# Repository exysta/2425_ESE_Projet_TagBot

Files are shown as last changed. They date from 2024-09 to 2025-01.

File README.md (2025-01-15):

# 2425_ESE_Project_TagBot
Welcome to the TagBot project created by the amazing team consisted of Lucas Chapart, Charlotte Fricot and Marie Caronello.
The following description is in french but you can find the english description there but it is not up to date for now :

- [English](README_english.md)

  # Sommaire
  
1. [Introduction](#introduction)
2. [PCB](#pcb)
3. [Code](#code)

  # Introduction
  
Vous vous trouvez actuellement dans le projet TagBot (ou robot chat), qui s'intègre à un projet de classe où chaque équipe doit concevoir un robot. Ces robots doivent pouvoir jouer au chat ensemble, avec un chat et des souris, sur une table sans bords. 
  
Au terme de ce projet, notre chat robot doit pouvoir:
 - se déplacer sur une table sans bordure (sans tomber)
 - changer d'état (chat ou souris)
  - si le robot est chat, il doit pouvoir attraper la souris
  - si le robot est souris, il doit pouvoir échapper au chat
  
Nous avons plusieurs niveaux d'objectifs à atteindre : 
  - Niveau 0 : le robot se déplace + ne tombe pas de la table
  - Niveau 1 : détection d'un robot et s'en rapprocher (chat) ou s'en éloigner (souris)
  - Niveau 2 : changement de comportement après un contact + fonctionnement avec plusieurs robots
  - Niveau 3 : capacité de se localiser + ne pas être affecté par les obstacles hors de la table

  Le projet doit être réalisé sur un semestre, du mois de septembre au mois de janvier, avec un certain nombre de livrables à fournir avant chaque étape clé. Les   différentes étapes techniques incluent des phases de conception, de développement et de validation sur un système embarqué.

  <details>
  <summary><strong>Plan détaillé</strong></summary>  

  ### Avant les vacances de la Toussaint
  
  Les 10 premières séances sont consacrées à la création du PCB que l'on doit commander avant les vacances de la Toussaint. 
  
  - Séance 1 → Schéma architectural / BOM
  - Séance 2 et 3 → Schéma électronique annoté
  - Séance 4 → Corrections Schéma / BOM Finale
  - Séance 5 → Placement
  - Séance 6 → Placement corrigé
  - Séance 7 → Routage
  - Séance 8, 9 et 10 → Corrections Routage, export

  Dans le même temps, nous avons débuté la partie informatique avec la création du projet sur CubeIDE. Nous avons configuré les pins et commencé la rédaction des librairies pour les différents composants. 

  ### Entre la Toussaint et Noël

  Cette période est centrée sur le développement logiciel et l'intégration.

  ### Après les vacances de Noël

  L'accent est mis sur les derniers ajustements et les tests finaux avant la présentation. En effet, les dernières séances consacrées à ce projet vont nous permettre de finaliser les algorithmes de stratégie et les comportements robotiques. Le challenge final aura lieu le vendredi 10 janvier, ce challenge consistera en un test et une présentation du projet où tous les robots chats de notre classe s'affronteront.

   </details>

  ## Schéma architectural et materiel

<div align="center">
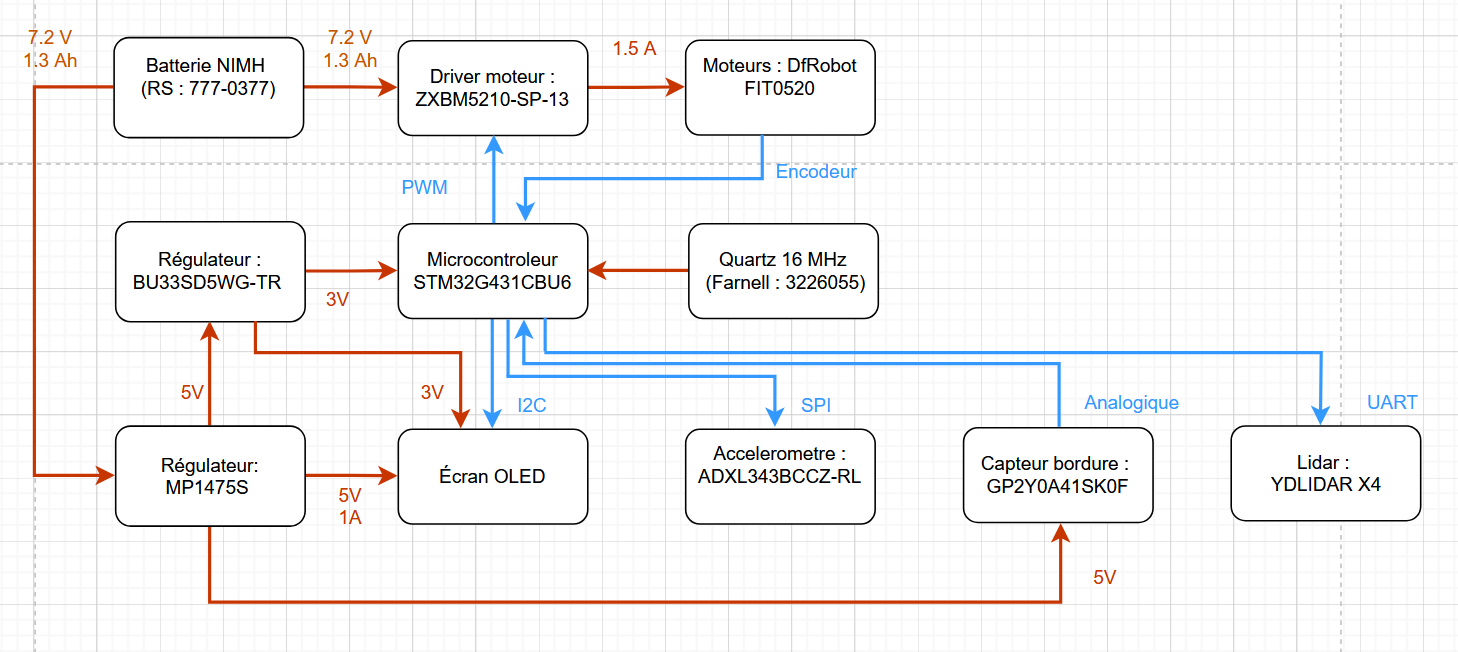
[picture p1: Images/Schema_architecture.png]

</div>
  
  L'essentiel du matériel a été imposé, mais il restait à déterminer le moyen par lequel le robot détecterait les bords pour éviter de tomber de la table. Pour cela, des capteurs infrarouges (IR) ont été choisis. Placés sous le robot, ces capteur reçoivent une tension qui détermine la distance par rapport au sol. Lorsque ce signal diminue fortement (ce qui correspond à une augmentation de la distance), cela indique la présence d'un bord. Étant donné que les capteurs sont situés sous le robot, il est nécessaire de détecter de faibles distances, comme le permet le capteur Sharp GP2Y0A21SK0F.

  Il est également envisagé d'ajouter une LED visible par l'utilisateur, permettant de connaître l'état du robot chat à tout moment.

  # PCB
  La première étape de la conception du PCB a été de réaliser le schéma électronique de la carte. Voici une liste des composants utilisés :

- **Microprocesseur** : STM32G431CBU6
- **Régulateurs de tension** : 5V et 3.3V
- **Drivers de moteurs** : ZXBM5210-SP-13
- **Système de batterie** : Batterie NIMH 7.2V 1.3Ah 
- **ST Link** : Interface de programmation et débogage
- **Oscillateur Quartz** : 16MHz
- **Connecteurs** : Divers connecteurs pour l'alimentation et les signaux
- **Accéléromètre** : ADXL343

## Détail des composants et branchements

### 1. Microprocesseur : STM32G431CBU6

Le microprocesseur STM32G431x6 est au cœur du robot. Il gère la logique du jeu et communique avec les autres composants. Le schéma de branchement du microprocesseur est disponible [ici](./Documents/datasheets/stm32g431cb.pdf).

<div align="center">
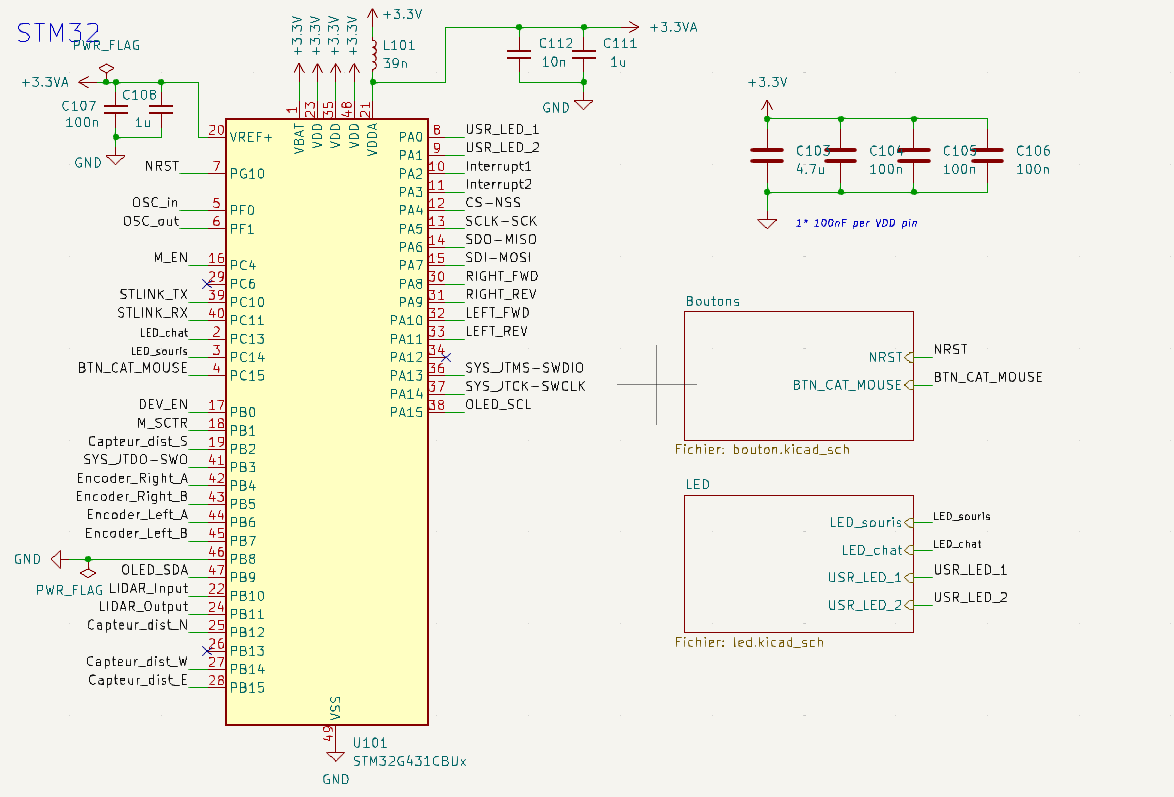
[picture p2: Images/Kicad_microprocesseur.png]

</div>

Les principaux branchements incluent :

- **VDDA** : Connecté à un filtrage LC pour lisser l'alimentation analogique.
- **VSS / VDD** : Alimentations principales.
- **GPIOs** : Utilisés pour le contrôle des LED de débogage et la communication avec les drivers de moteur.

Pour configurer les broches du microcontrôleur, le logiciel CubeIDE est utilisé. Une fois la configuration effectuée, la génération du fichier `.ioc` permet de documenter l'ensemble des options choisies pour chaque broche. Le fait d'utiliser l'ioc du microprocesseur permet de choisir au mieux chaque broche pour les entrée/sortie du microprocesseur.

### 2. LED

Le robot comporte 7 LEDs connectées à des résistances de limitation de courant.

- **Une LED rouge** : indique que le robot est le chat.
- **Une LED Bleue** : indique que le robot est une souris.
- **Deux LED vertes** : sont des LEDs de débogage.
- **Une LED jaune** : 5V
- **Une LED verte** : 3.3V
- **Une LED verte** : 7.2V

<div align="center">
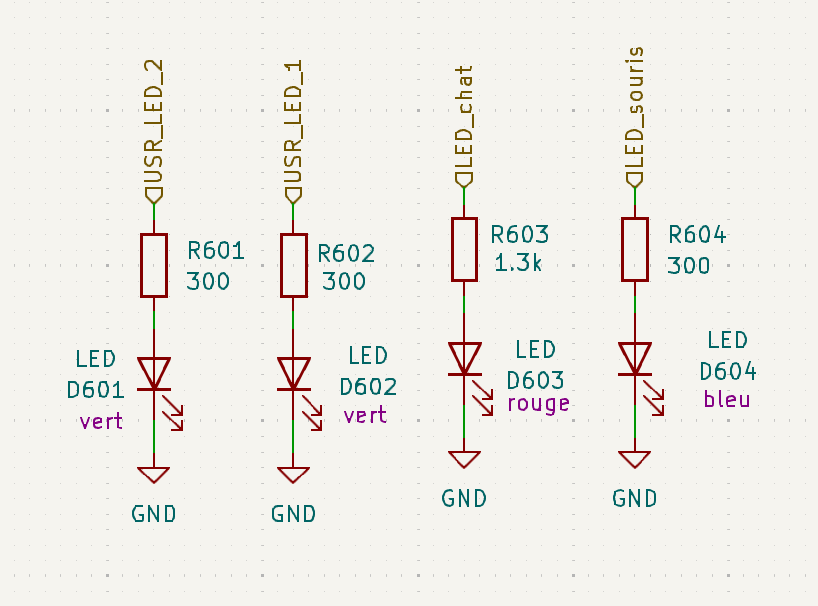
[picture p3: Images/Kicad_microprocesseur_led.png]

</div>

### 3. Boutons

Le robot dispose de deux boutons :

- **NRST** : Bouton de réinitialisation.
- **Mode** : Bouton qui permet de changer l'état du robot entre "chat" et "souris".

<div align="center">
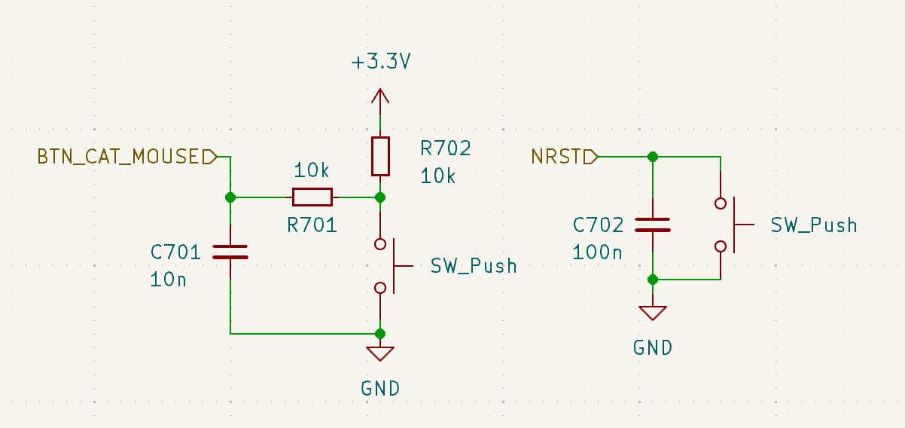
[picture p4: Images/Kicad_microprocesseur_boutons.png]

</div>

### 4. Drivers de Moteurs : ZXBM5210-SP-13

Les drivers de moteurs permettent de contrôler les moteurs à courant continu utilisés pour déplacer le robot. Le driver ZXBM5210 est connecté selon le schéma de la [documentation](./Documents/datasheets/driver_ZXBM5210.pdf).

<div align="center">
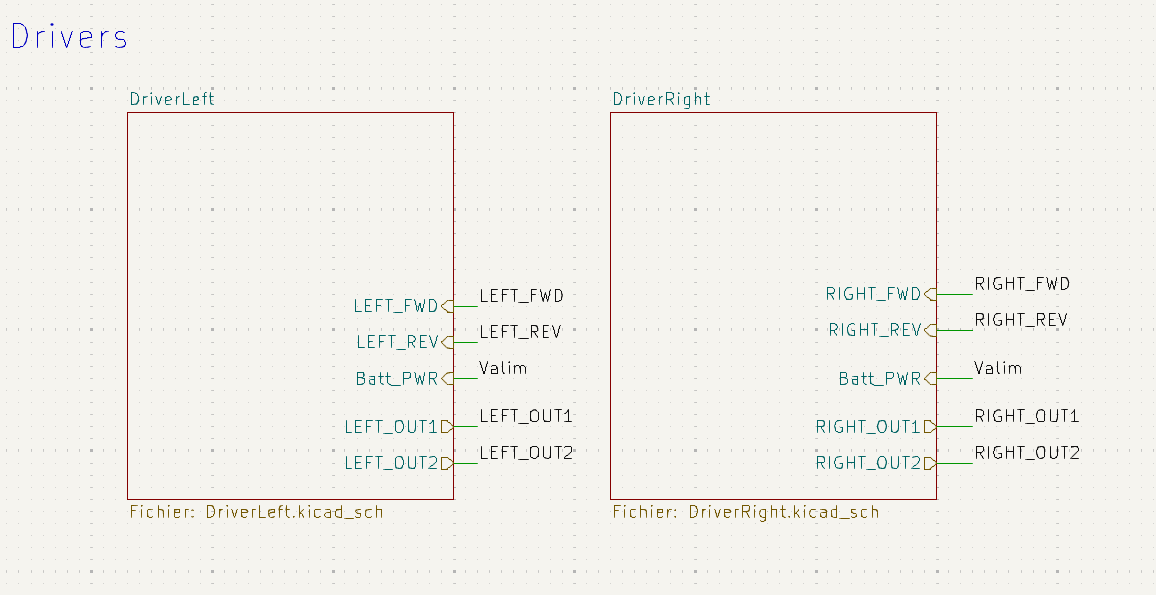
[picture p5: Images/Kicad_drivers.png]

</div>

Le branchement des drivers inclut :

- **Vref** : Tension de référence pour le contrôle de vitesse
- **VDD** : Alimentation des moteurs
- **Entrées de contrôle** : Connectées aux GPIOs du microprocesseur

<div align="center">
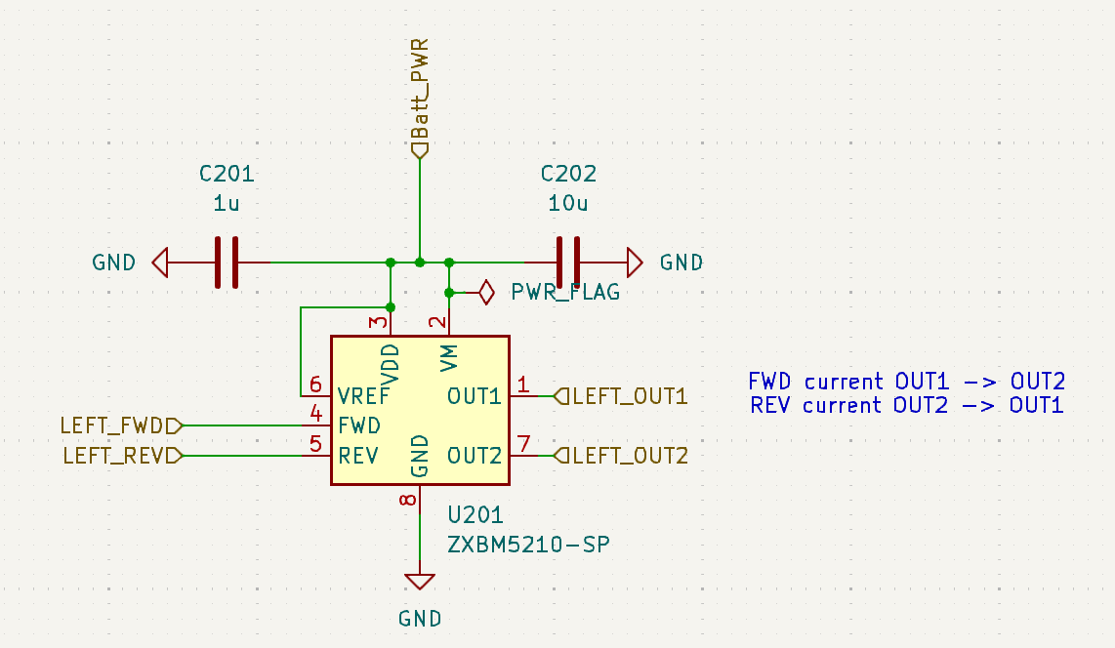
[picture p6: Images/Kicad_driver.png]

</div>

### 5. Régulateurs de Tension

Deux régulateurs de tension sont utilisés pour convertir l'alimentation de la batterie :

<div align="center">
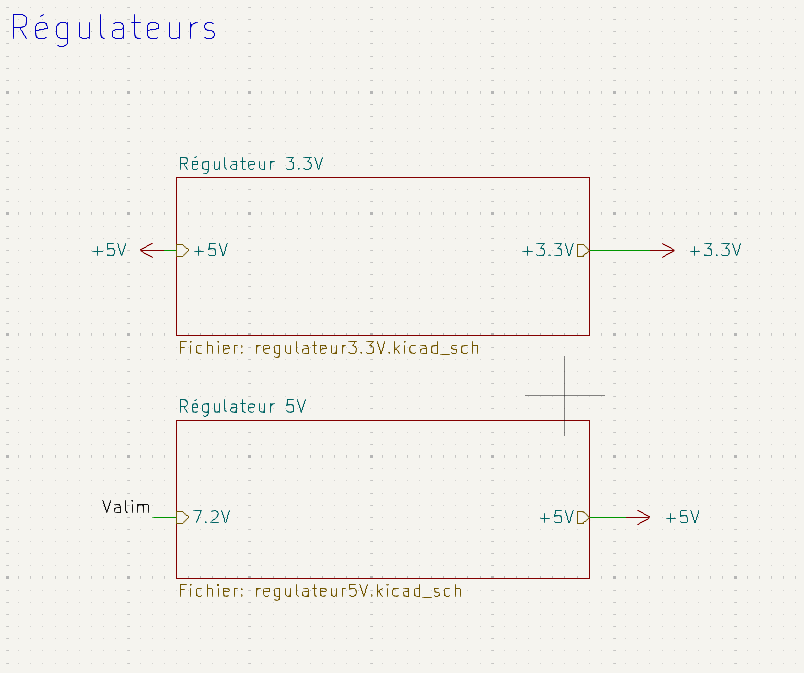
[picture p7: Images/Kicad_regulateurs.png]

</div>

1. **Régulateur 7.2V → 5V : MP1475S**
   - Construit selon la [documentation](./Documents/datasheets/regulateur_MP1475S.pdf).
   - Assure une tension de 5V en sortie pour l'alimentation du LIDAR et des capteurs de bords.
   - Concernant la résistance R = 7.68k, cette valeur est disponible et a donc été conservée. Si cela n’avait pas été le cas, il aurait été nécessaire de réaliser un diviseur de tension pour déterminer les valeurs des résistances permettant d'obtenir une sortie de 5V et 3A.
   - Pour vérifier la présence de la tension de 5V, une LED jaune a été ajoutée, et a été connectée à une résistance de limitation de courant.

<div align="center">
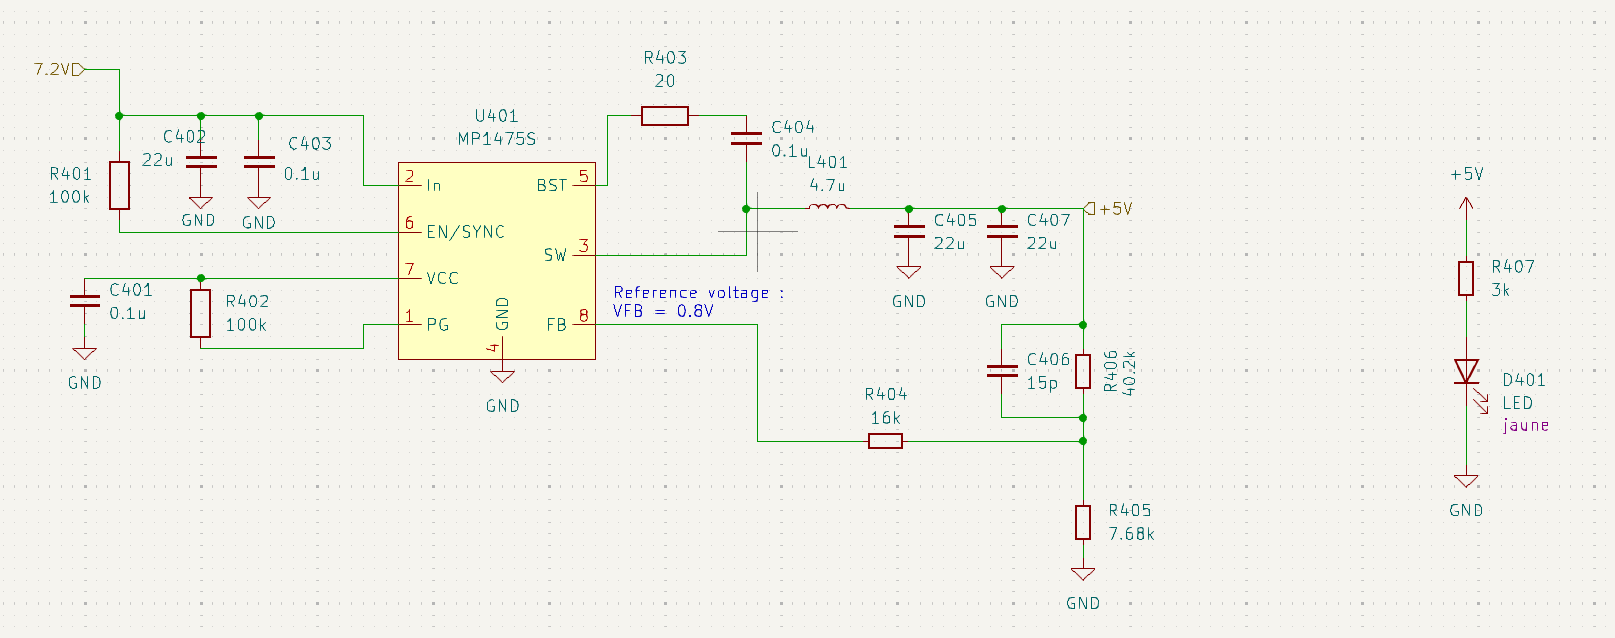
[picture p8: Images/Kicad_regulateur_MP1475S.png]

</div>

2. **Régulateur 5V → 3.3V : BU33SD5WG-TR**
   - Construit selon la [documentation](./Documents/datasheets/regulateur_buxxsd5wg-e.pdf).
   - Alimente le microprocesseur et l'écran en 3.3V.
   - Pour vérifier la précence de la tension de 3V, une LED verte a été ajoutée et a été connectée à une résistance de limitation de courant.

<div align="center">
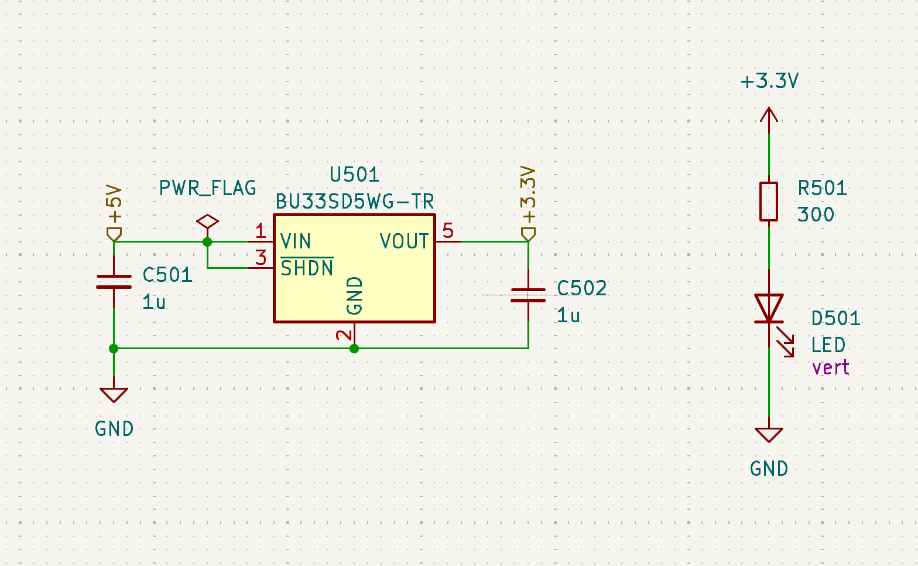
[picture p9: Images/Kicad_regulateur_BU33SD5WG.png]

</div>

### 6. Oscillateur Quartz 16MHz

L'oscillateur quartz est utilisé pour fournir une horloge stable au microprocesseur. Il est connecté selon le schéma standard, avec des condensateurs de découplage.

<div align="center">
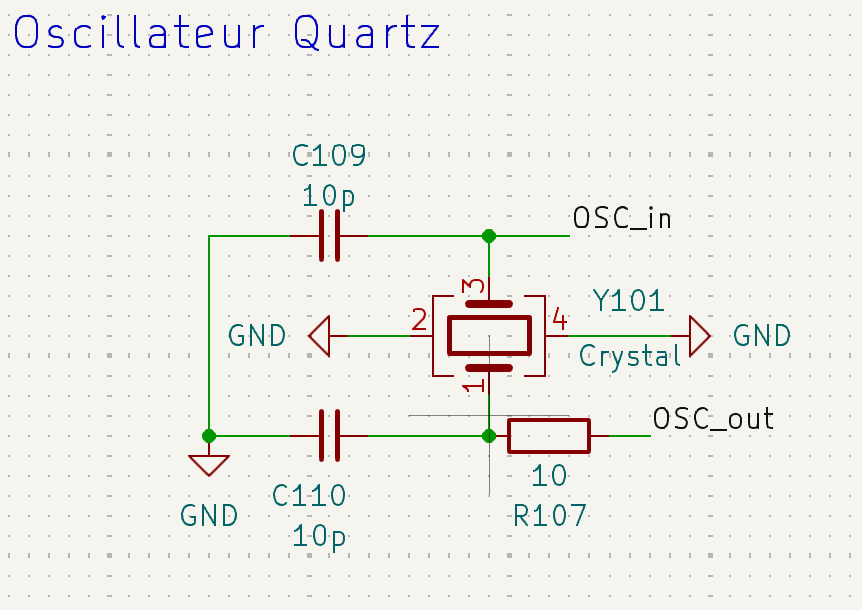
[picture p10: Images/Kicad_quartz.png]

</div>

### 7. ST Link

La ST Link est utilisée pour la programmation et le débogage du microprocesseur STM32. Elle permet de flasher le code sur le microprocesseur et d'assurer une communication série pour le débogage.

- **VCC** : Alimentation de la ST Link (3.3V).
- **SWDIO / SWCLK** : Broches de communication pour le débogage.
- **NRST** : Connecté au bouton de réinitialisation pour permettre un reset matériel lors de la programmation.

<div align="center">
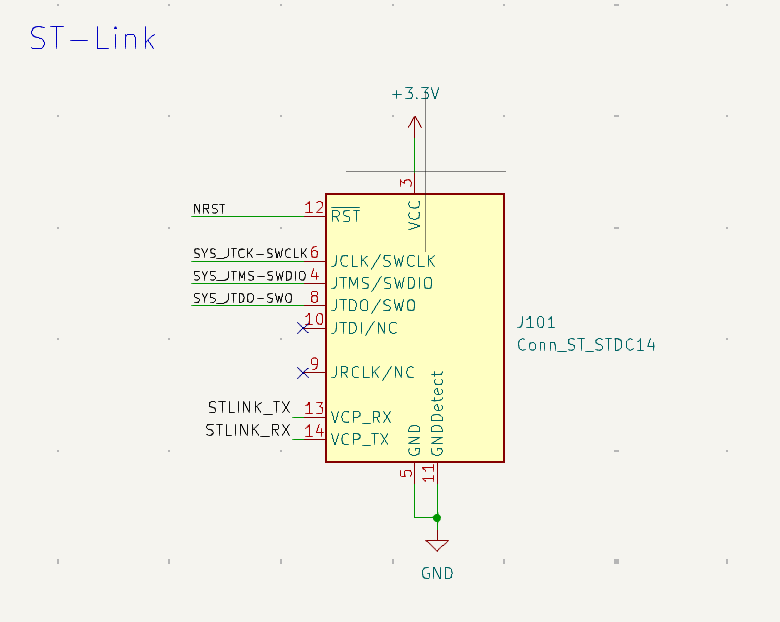
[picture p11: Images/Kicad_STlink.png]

</div>

### 8. Accéléromètre : ADXL343

L'accéléromètre ADXL343 permet de mesurer les mouvements du robot. Il est connecté au microprocesseur via une communication **SPI**. La configuration SPI a été choisie car elle offre une communication plus rapide et fiable dans notre application. Le schéma de branchement est basé sur la [documentation](./Documents/datasheets/accelerometre_adxl343.pdf).

<div align="center">
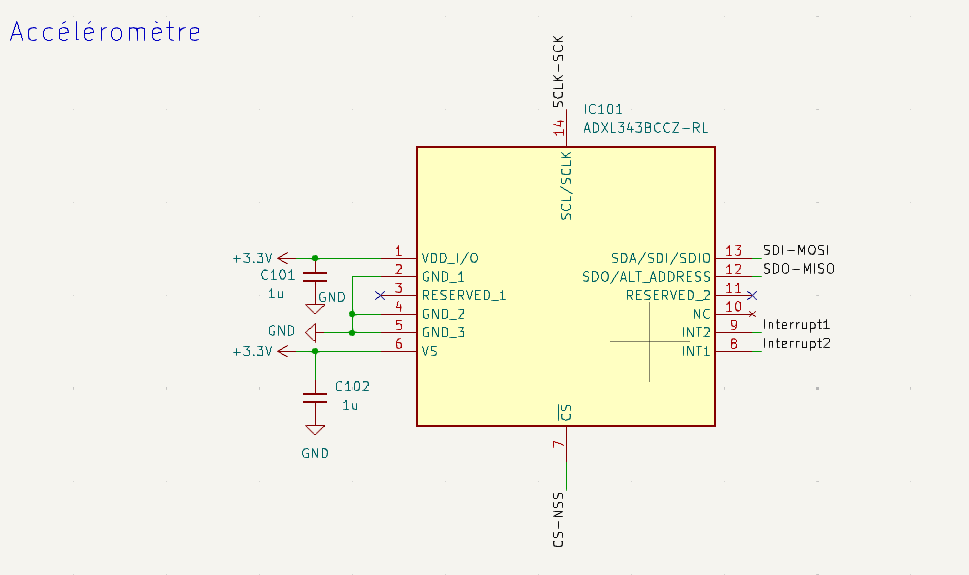
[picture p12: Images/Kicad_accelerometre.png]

</div>

### 9. Connecteurs

Le robot dispose de plusieurs connecteurs pour interfacer différents périphériques :

<div align="center">
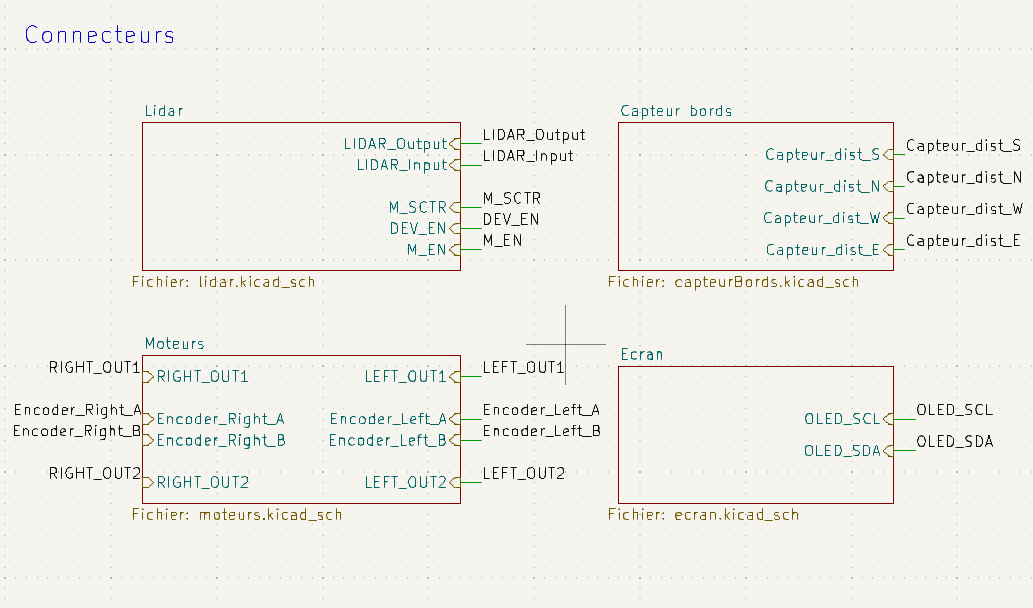
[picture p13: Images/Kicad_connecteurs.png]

</div>
 
1. **Connecteur Moteurs**

- Les connecteurs moteurs permettent de relier le PCB aux moteurs DC utilisés pour déplacer le robot.
- Chaque connecteur est relié à un driver de moteur ZXBM5210 pour gérer la vitesse et la direction.

<div align="center">
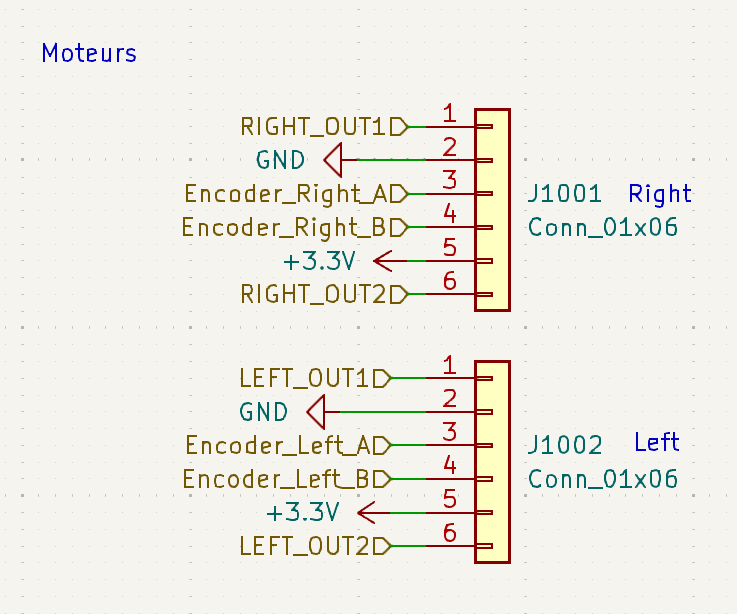
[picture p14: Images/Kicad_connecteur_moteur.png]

</div>

2. **Connecteur LIDAR**

- Le connecteur Lidar est utilisé pour interfacer un capteur Lidar au robot, permettant la détection de la distance et des obstacles.
- Il est connecté à l'un des ports de communication du microprocesseur (SPI ou UART).

<div align="center">
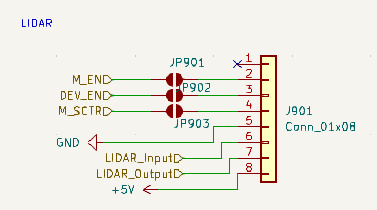
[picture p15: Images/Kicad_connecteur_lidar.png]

</div>

3. **Connecteur Écran**

- Le connecteur écran permet d'ajouter un petit écran pour afficher l'état du robot (chat ou souris).
- Ce connecteur est relié à l'interface I2C du microprocesseur.

<div align="center">
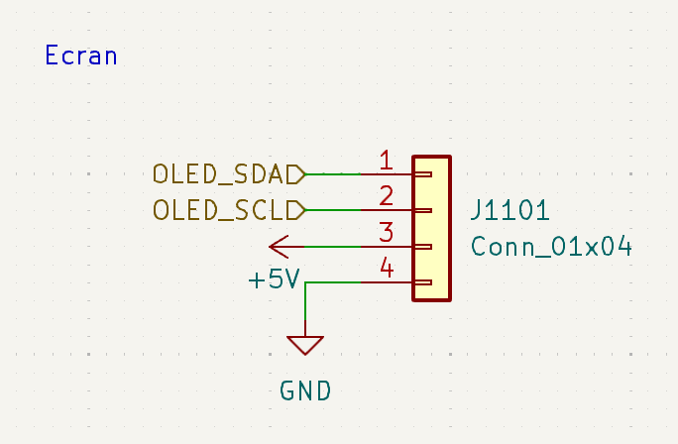
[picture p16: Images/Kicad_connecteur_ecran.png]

</div>

4. **Connecteur Capteur Bords**

- Le capteur bords est utilisé pour détecter les bords de la table et éviter que le robot ne tombe.
- Le capteur est relié intrinséquement à un ADC.

<div align="center">
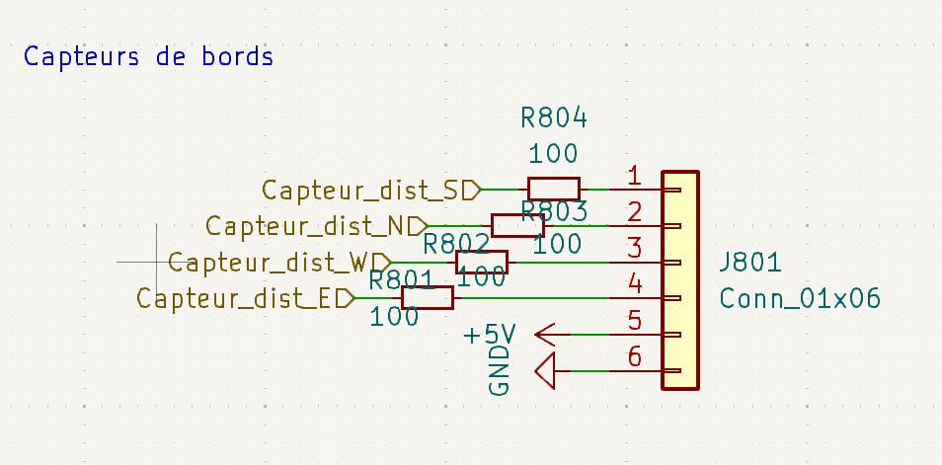
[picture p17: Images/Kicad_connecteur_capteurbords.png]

</div>

### 10. Batterie

Le robot est alimenté par une batterie LiPo de 7.2V, qui fournit de l'énergie aux régulateurs de tension pour les différents composants du circuit, la documentation utilisé est [ici](./Documents/datasheets/batterie_0900766b81582941.pdf). Pour vérifier la présence de la tension de 7.2V, une LED verte a été ajoutée et connectée à une résistance de limitation de courant.

<div align="center">
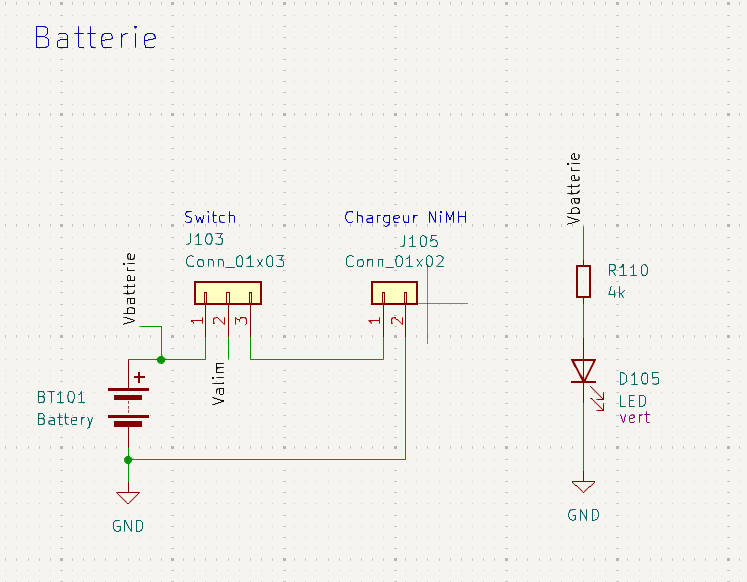
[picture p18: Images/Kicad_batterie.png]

</div>

## Ajustements à considérer pour un routage optimal
<details>
  <summary><strong> Détails</strong></summary>
  
### Répartitions des roles des couches du PCB

Répartition des 4 couches du PCB :
- **Couche 1 (Front)** :
Couche sur laquelle sont placés tous nos composants, la plupart étant en CMS, à l'exception des connecteurs qui sont en traversants. La majoté des pistes de données se trouvent sur cette couche, tandis qu'une partie d'entre elles passent par la couche bottom. Cela permet de maintenir l'homogénéité des plans de masse (couche 2) et d'alimentation (couche 3), ce qui protège l'intégrité des signaux de données.
  
- **Couche 2** :
Plan de masse. Il est important d'espacer nos vias pour ne pas couper le plan de masse.
  
- **Couche 3** :
Couche d'alimentation. Elle contient les plans d'alimentations pour les composants à forte consommation de puissance. Cela permet une meilleure dissipation thermique.
  
- **Couche 4 (Bottom)** :
Une partie des pistes de données ainsi que les points de test se situent sur cette couche. Lors du routage des pistes sur cette couche, il faut essayer de ne pas faire passer les pistes par les discontinuités des plans d'alimentations présents sur la couche 3. En effet, cette discontinuité peut poser des problèmes de CEM pour les signaux de données les plus rapides tels que : UART, I2C, SPI et signaux de debug.
  
### Bonnes pratiques pour les plans

- **Attention aux antennes** :
Les pistes ou zones de cuivre non connectées peuvent se comporter comme des antennes et générer des interférences électromagnétiques (EMI). Pour minimiser ce risque, il est essentiel d’éviter la création de segments de cuivre flottants, en particulier dans les plans de masse et d’alimentation. Sur l'image ci-dessous, des antennes sont visibles. Ce problème peut être évité en ajoutant des vias aux extrémités de ces antennes ou en définissant une zone d'exclusion pour empêcher le remplissage.

<div align="center">
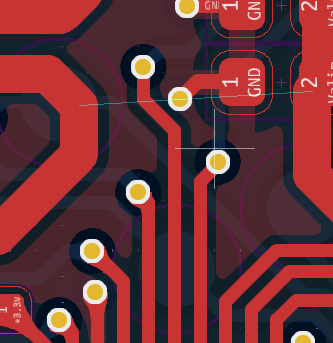
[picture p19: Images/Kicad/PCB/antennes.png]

</div>

- **Éviter les discontuinités des plans de masse** :
Les interruptions dans les plans de masse peuvent créer des chemins de retour de courant indésirables, affectant la performance globale du circuit, notamment pour les signaux à haute fréquence. Un plan de masse continu garantit un retour propre des courants et prévient les problèmes d’intégrité du signal. Il est recommandé de s'assurer que les pistes de signal, d’alimentation ou les vias ne créent pas de coupures dans ce plan, comme on peut le voir sur l'image ci-dessous.

<div align="center">
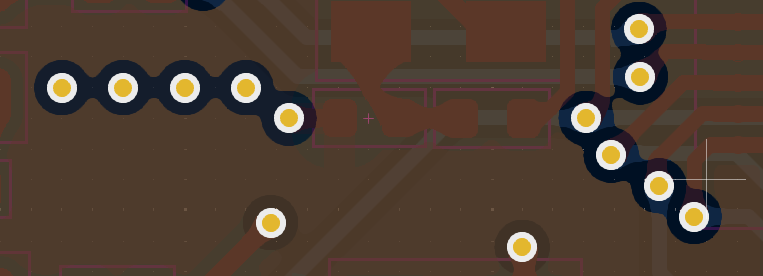
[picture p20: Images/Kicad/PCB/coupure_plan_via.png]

</div>

### Bonnes pratiques pour les pistes et vias

- **Placer les vias proches des pads lorsque cela est possible** :
Les vias doivent être placés aussi près que possible des pads des composants pour réduire la longueur des pistes et ainsi limiter l'inductance parasite.

<div align="center">
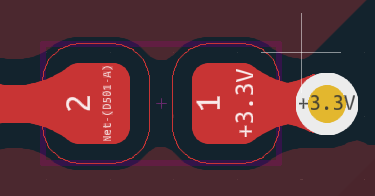
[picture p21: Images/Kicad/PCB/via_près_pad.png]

</div>
  
- **Adapter la largeur des pistes en fonction du type de signal pour des raisons thermiques**:
Il est important de dimensionner correctement la largeur des pistes selon le type de courant qui les traverse. Les pistes de puissance, par exemple, doivent être suffisamment larges pour assurer une bonne dissipation thermique et limiter les pertes résistives. Une largeur insuffisante pourrait entraîner une surchauffe ou une dégradation des performances du circuit. À l'inverse, les pistes de signal, qui véhiculent des courants plus faibles, peuvent être plus fines.

<div align="center">
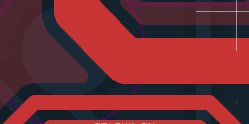
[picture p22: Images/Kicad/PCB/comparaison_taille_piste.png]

</div>

- **Éviter les angles droits ou inférieurs à 90° sur les pistes** :
Les pistes présentant des angles droits ou très aigus peuvent entraîner des discontinuités d’impédance, causant des réflexions de signal et des perturbations électromagnétiques, notamment dans les circuits haute fréquence. Ces angles peuvent également constituer des points de faiblesse thermique ou mécanique. Il est recommandé d’utiliser des angles de 45° ou des courbes douces pour maintenir la continuité du signal et réduire les effets de réflexion et d’interférence.

- **Position des vias par rapport aux pastilles de brasage**:
Sur l'image ci-dessous, les vias ne sont pas placés directement sur les pastilles de brasage. Cette configuration a été choisie pour éviter des problèmes de soudure et pour permettre une meilleure dissipation thermique.

<div align="center">
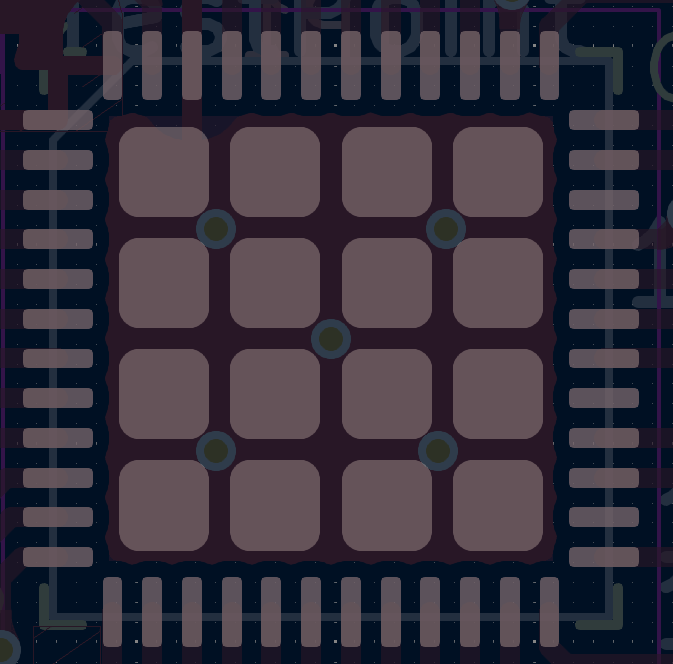
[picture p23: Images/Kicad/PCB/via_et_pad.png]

</div>

###  Bonnes pratiques pour les composants

- **Condensateurs de découplage à faible valeur** :
Les condensateurs de plus petite capacité (souvent des céramiques, typiquement dans les gammes de 100nF à 1µF) sont destinés à filtrer les hautes fréquences et doivent être placés aussi près que possible des pins d'alimentation des composants. Leur faible constante de temps leur permet de répondre rapidement aux fluctuations rapides de la tension causées par des commutations rapides dans les circuits numériques.

- **Condensateurs de plus grande valeur**:
Les condensateurs de plus grande capacité (souvent dans les gammes de 10µF à 100µF ou plus, et souvent des électrolytiques ou des tantales) servent à fournir une énergie plus conséquente pour des fluctuations de tension plus lentes, mais ne sont pas aussi efficaces pour les hautes fréquences. Ils peuvent être placés un peu plus loin des composants, mais idéalement, ils devraient rester dans le même plan d'alimentation. Leur rôle est de compléter les condensateurs de faible valeur, en offrant une stabilisation à des fréquences plus basses.

### Tests points
L'ajout de points de test accessibles facilite la vérification des tensions d'alimentation, des signaux critiques ou d'autres tests en cours de fabrication et de débogage.

</details>

# Code

  ## Documentation Code
Le détail des fonctions structures et autres peuvent être visualiser en utilisant la documentation Doxygen :

[voir la documentation Doxygen](https://exysta.github.io/2425_ESE_Projet_TagBot/Documents/Doxygen_Documentation/html/index.html)

La documentation qui suit est un résumé du fonctionement et ne rentre pas trop dans les détails déjà couvert par la documentation DOxygen.
  
  ## Introduction

  Dans le cadre du projet, nous devons utiliser plusieurs moyens de communications tels que le SPI pour l'accéléromètre, l'I2C pour l'écran OLED, l'UART pour le lidar et une lecture de tension avec un ADC pour les capteurs de distance.

  ## FreeRTOS config 
  
  

  ## Task Priority
  - Motor task = 11
  - Distance sensor task = 10
  - Robot strategy task = 9
  - Accelerometer task = 8
  - Lidar task = 7
  - Shell task = 6

  Cette ordre de priorité nous permet de nous assurer un controle des moteurs prioritaire est assure une bonne détection d'un potententiel vide par notre tâche Distance sensor
## exemple d'utilisation dans un main.c
  ```c
/* USER CODE BEGIN Includes */
#include "stm32g4xx_hal.h"
#include "semphr.h"
#include "X4LIDAR_driver.h"
#include "DCMotor_driver.h"
#include "SSD1306.h"
#include "SSD1306_fonts.h"
#include "shell.h"
#include "RobotStrategy.h"
#include "distSensor_driver.h"
#include "ADXL343_driver.h"

/* USER CODE BEGIN PV */
X4LIDAR_handle_t X4LIDAR_handle;
DualDrive_handle_t DualDrive_handle;
__TARGET_HandleTypeDef Target_Handle;

int main(void)
{
...

	printf(" _____________________________\r\n");
	printf("|                             |\r\n");
	printf("|                             |\r\n");
	printf("|  WELCOME ON TAGBOT PROJECT  |\r\n");
	printf("|                             |\r\n");
	printf("|_____________________________|\r\n");
	//**********************************************************

	/* Ce code initialise l'adc en dma*/
	distSensor_TaskCreate(NULL);
	printf("Démarrage du test des capteurs de distance...\r\n");

	//**********************************************************

	/* Code init l'accélérometre*/

	ADXL343_TaskCreate(NULL);
	printf("adxl task creat \r\n");

	//**********************************************************
	DCMotor_CreateTask(&DualDrive_handle);
	printf("dcmotor task creat \r\n");

	//**********************************************************
	// Init SCREEN OLED
	if(HAL_OK == SCREEN_SSD1306_Init(&hscreen1, &hi2c1))
	{
		SCREEN_SSD1306_DrawBitmap(&hscreen1, Nyan_115x64px, 115, 64, White);
		//SCREEN_SSD1306_DrawBitmap(&hscreen1, Jerry_50x64px, 120, 64, White);
		SCREEN_SSD1306_Update_Screen(&hscreen1);
	}
	//**********************************************************
	//LIDAR

	X4LIDAR_create_task(&X4LIDAR_handle);
	printf("lidar task creat \r\n");
	//**********************************************************

	RobotStrategy_CreateTask();

	//**********************************************************

	printf("Tasks creation finished... \r\n");
	//**********************************************************

  /* USER CODE END 2 */

  /* Call init function for freertos objects (in cmsis_os2.c) */
  MX_FREERTOS_Init();

  /* Start scheduler */
  osKernelStart();
...
}
void HAL_UART_RxHalfCpltCallback(UART_HandleTypeDef *huart)
{

	X4LIDAR_HAL_UART_RxHalfCpltCallback(huart,&X4LIDAR_handle);

}

void HAL_UART_RxCpltCallback(UART_HandleTypeDef *huart)
{

	shell_drv_uart_HAL_UART_RxCpltCallback(huart);
	X4LIDAR_HAL_UART_RxCpltCallback(huart,&X4LIDAR_handle);

}

void HAL_UART_TxCpltCallback(UART_HandleTypeDef *huart)
{
	shell_drv_uart_HAL_UART_TxCpltCallback(huart);
}
/* USER CODE END 4 */

/**
  * @brief  Period elapsed callback in non blocking mode
  * @note   This function is called  when TIM7 interrupt took place, inside
  * HAL_TIM_IRQHandler(). It makes a direct call to HAL_IncTick() to increment
  * a global variable "uwTick" used as application time base.
  * @param  htim : TIM handle
  * @retval None
  */
void HAL_TIM_PeriodElapsedCallback(TIM_HandleTypeDef *htim)
{
  /* USER CODE BEGIN Callback 0 */

  /* USER CODE END Callback 0 */
  if (htim->Instance == TIM7) {
    HAL_IncTick();
  }
  /* USER CODE BEGIN Callback 1 */
	  DCMotor_EncoderCallback(htim ,&DualDrive_handle);

  /* USER CODE END Callback 1 */
}
````

  ## Pilote X4 LIDAR

  ### Aperçu
  Cette implémentation est un pilote pour le capteur X4 LIDAR, conçu pour fonctionner sur des systèmes embarqués utilisant FreeRTOS. Le pilote gère la communication avec le capteur LIDAR via UART et fournit des fonctionnalités pour la configuration du dispositif, le balayage et le traitement des données.
  
  ### Fonctionnalités
  - Communication UART avec le capteur X4 LIDAR
  - Récupération des informations du dispositif (modèle, firmware, version matérielle, numéro de série)
  - Opérations de balayage avec support DMA
  - Gestion des tâches FreeRTOS
  - Analyse et validation des en-têtes de réponse
  - Détection et traitement efficace des trames de données
  
  ### Dépendances
  - FreeRTOS
  - STM32 HAL (Hardware Abstraction Layer)
  - Bibliothèques C standard (stdlib.h, math.h)
  
  ### Fonctions Principales
  - `X4LIDAR_init`: Initialise le pilote LIDAR et effectue la configuration initiale
  - `X4LIDAR_start_scan`: Démarre le processus de balayage LIDAR
  - `X4LIDAR_get_device_info`: Récupère les informations du dispositif
  - `X4LIDAR_create_task`: Crée une tâche FreeRTOS pour les opérations LIDAR
  - `X4LIDAR_send_command`: Gère la transmission des commandes au capteur
  
  ### Exemple d'Utilisation
  main.c:
  ```c
  // Initialisation de la structure LIDAR
  X4LIDAR_handle_t lidar_handle;
  UART_HandleTypeDef huart3;  // Votre handle UART
  
  // Création de la tâche LIDAR
  X4LIDAR_create_task(&lidar_handle);
  /* Start scheduler */
  osKernelStart();

void HAL_UART_RxHalfCpltCallback(UART_HandleTypeDef *huart)
{

	X4LIDAR_HAL_UART_RxHalfCpltCallback(huart,&X4LIDAR_handle);

}

void HAL_UART_RxCpltCallback(UART_HandleTypeDef *huart)
{
	X4LIDAR_HAL_UART_RxCpltCallback(huart,&X4LIDAR_handle);
}

````
X4LIDAR_driver.c:
  ```c
//ensure the correct uart is used for the init
void X4LIDAR_task(void *argument)
{
    // Retrieve the LiDAR handle passed as argument
    X4LIDAR_handle_t *X4LIDAR_handle = (X4LIDAR_handle_t*) argument;

    // Initialize the LiDAR hardware
    X4LIDAR_init(X4LIDAR_handle, &huart3);
    X4LIDAR_start_scan(X4LIDAR_handle);
...
}
````
For the uart config : 



For the DMA config :



## Robot Strategy

Ce fichier a pour but de centraliser et synchroniser les différentes fonctionalitées du robot. C'est dans ce fichier que le traitement des donnés du Lidar est fait pour déterminer la cible la plus proche.On y gère également les états chat/souris.

Idéalement il aurait fallu tout centraliser sur cette tache mais par manque de temps et pour s'assurer que les actions critiques telles que le freinage des moteurs se faisaient à temps, une partie à des actions s'effectuent dans les autres taches.

## DC Motor Driver
Ce fichier contient des fonctions pour controler les pwm envoyer aux deux moteurs. Il contient également les fonctions pour les encodeurs des moteurs.

Une petie rampe pour les pwm a été utilisé et l'acquisition de la vitesse des moteurs se fait toutes les secondes via le callback d'un timer.

## Shell

La shell est uniquement utilisé pour le debug étant donné que la connexion STLink n'est pas possible si le robot doit se déplacer. 
des fonctions peuvent y etre ajouté en appellant shell_add(). exemple d'utilisation :

  ```c
	shell_init(&h_shell);
	shell_add(&h_shell, "print_dist", print_lidar_distances,
			"print lidar buffer containing scanned distances");
	shell_add(&h_shell, "print_motor_speed", print_motor_speed,
		"print_motor_speed");
	shell_createShellTask(&h_shell);
	...
  /* Start scheduler */
  osKernelStart();
````
## L'écran OLED SSD1306
L'écran est uniquement utilisé pour le fun afin d'avoir un moyen de visualiser si le robot est en mode chat ou sours. La librairie utilisé à été légérement adapté pour prendre en charge l'affichage d'images.

cat

## L'accéléromètre ADXL343
  
  Nous allons à présent établir le code pour l'accéléromètre ADXL343, il va permettre de déteter un TAP et donc un changement d'état du robot, lorsque ce dernier entre en collision avec un autre robot. Pour pouvoir communiquer avec l'ADXL343 nous allons utiliser la communication SPI, ainsi on va définir deux fonctions principale pour lire et ecrire dans les registres. 
  
  ### Paramètres
  
  Dans le header en plus de définir les différents registres qui seront utilisés dans le code, et les différents structures, on peut également définir des paramètres clés pour la détection du TAP tel que :
  
  ````ruby
  #define TAP_THRESHOLD 			0x20											
  #define TAP_DURATION 			0x10 										
  #define TAP_LATENT 				0xC8
  ````
  
  On définit alors le seuil de détection du tap ici 2g, la durée entre deux tap différents ici 10ms et la durée total d'un single TAP.
  
  ### Lire et Ecrire dans les registres
  
  Pour pouvoir lire dans les registres on doit d'abord activer le NSS, ensuite on envoie l'adresse à laquelle on veut lire la donnée, puis on lit la donnée associée à l'adresse du registre et enfin on désactive le NSS. 
  
  ````ruby
  void ADXL343_ReadRegister(uint8_t reg, int8_t* rx_data, size_t length)
  ````
  
  De la même manière pour écrire dans un registre on active le NSS ensuite on transmet les données que que l'on veut transmettre dans le registre qui nous intéresse et puis on désactive le NSS.
  
  ````ruby
  void ADXL343_WriteRegister(uint8_t reg, uint8_t data)
  ````
  
  ### Initialisation de l'accéléromètre
  
  Pour l'initialisation de l 'accéléromètre, on commence tout d'abord en vérifiant que la connexion est corréctement établit, pour cela on vérifie que la valeur du registre ADXL343_REG_DEVID est bien 0xE5. Ensuite on configure les différents registres pour mettre l'accéléromètre en mode veille, définir le format des données, et activer le mode mesure.
  
  ````ruby
  int ADXL343_Init(ADXL343_Handle_t* handle)
  ````
  
  Ensuite on va spécifiquement configurer les seuils, la durée, et les axes pour détecter les tapotements. On va également activer les interruptions pour les événements de tapotement simple sur n'importe quel axe.
  
  ````ruby
  void ADXL343_Configure(ADXL343_Handle_t* handle)
  ````
  
  ### Détection du TAP
  
  Le but de l'accéléromètre est de détecter lorsque le robot entre en collision pour ensuite pouvoir changer d'état. Pour cela on va lire la valeur du registre ADXL343_REG_INT_SOURCE et lorsque le 6 eme bit est à 1 cela signifie que l'on a détecter un single TAP.
  
  ````ruby
  void ADXL343_DetectTap(ADXL343_Handle_t* handle)
  ````
  
  ### Détection du TAP dans une tâche
  
  Avec l'activation de freeRTOS le fonctionnement est géré dans une tâche périodique permettant une exécution asynchrone et une intégration facile dans un système temps réel.
  
  ````ruby
  void ADXL343_TaskCreate(void * unused)
  ````

  ## Capteurs de distance
  
  Dans cette partie on va expliquer le code pour les capteurs de distance. Les capteurs de distance vont permettre de détecter le vide et ainsi d'arréter les moteurs pour éviter que le robot tombe de la table. On va donc utiliser 4 capteurs Nord, West, Sud, Est on utilisera deux canaux ADC1 et ADC2 sur la STM32. ADC1 lit les capteurs de distance situés à l'ouest (west) et au nord et ADC2 lit les capteurs de distance situés au sud et à l'est. Chaque capteur est représenté par une structure(DistSensor_handle_t) qui contient des informations telles que l'état du capteur et les valeurs mesurées. Les données des ADC sont transférées en mémoire via DMA pour améliorer les performances et réduire la charge du CPU.
  
  ### Initialisation
  
  Pour l'initialisation on va démarrer les conversions ADC en mode DMA pour ADC1 et ADC2 et activer le timer associé htim6 pour synchroniser les conversions. On initialise les capteurs avec les valeurs par défaut.
  
  ````ruby
  void distSensor_initADC_DMA(void)
  ````
  
  ### Lire les valeurs de l'ADC
  
  On va lire les valeurs de l'adc pour pouvoir déterminer si la distance qu'on évalue de l'objet le plus proche est le vide ou pas. On établit deux fonctions l'une en mode polling tel qu'on effectue la lecture manuelle d'une valeur ADC en mode blocant. Mais on établie aussi la focntion de lecture des données en mode DMA. La lecture des données des buffers DMA  s'éffectue pour chaque capteur avec la mise à jour des états  en fonction d'un seuil (VOID_TRESHOLD). On vérifie si le capteur détecte un sol ou du vide .
  
  ````ruby
  uint32_t distSensor_ReadADC(ADC_HandleTypeDef* hadc)
  ````
  
  ````ruby
  HAL_StatusTypeDef distSensor_ReadADC_DMA(void)
  ````
  
  On appelle la fonction CallBack lorsque la conversion ADC est terminée. 
  ````ruby
  void HAL_ADC_ConvCpltCallback(ADC_HandleTypeDef *hadc)
  ````
  
  ### Fonctionnement des capteurs de distance en tâche
  
  On commence par créer une fonction exécutée en tâche FreeRTOS pour gérer les capteurs en continu, cette fonction va lit les données des capteurs via la fonction évoquée précédemment et on vavérifier si un ou plusieurs capteurs détectent du vide. Si oui, on déclenche une procédure d'arrêt d'urgence en activant le freinage des moteurs, et on réinitialise leur vitesse à 0 après un délai. L'arret d'ugence s'effectue directement ici pour éviter d'éventuels délais/préemption qui pourrait ralentir l'arret.
  
  ### Note Bonus
  Attention, il faut penser à mettre le continuous conversion mode de l'adc en disable sinon le programme bloque.
  
  Autre point important, les adc sont sur 12 bits, il est donc préférable de configurer le dma pour le transfert de half-word i.e 16 bits. Cependant, il faut alors penser à définir le buffer du DMA comme uint16_t adc1_dma_buffer[ADC1_CHANNEL_COUNT];.
  
  En effet, si l'on défini le buffer avec des uint32_t, les valeurs de 2 channels sur 16 bits se retrouveront concaténées sur une valeur de 32 bits. Pour des raisons obsucre il y avait encore des bugs de cette facon.
  
  En mettant les transferts du dma en format word avec  uint32_t adc1_dma_buffer[ADC1_CHANNEL_COUNT] cela semble régler le problème.

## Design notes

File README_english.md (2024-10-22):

# Table of Contents

1. [Introduction](#introduction)
2. [PCB](#pcb)
3. [Code](#code)

# Introduction

You are currently in the TagBot project (or robot cat), which is part of a class project where each team must design a robot. These robots are meant to play tag together, with a cat and mice, on a table without edges.

At the end of this project, our robot cat must be able to:
- Move on a table without edges (without falling off)
- Change state (cat or mouse)
    - If the robot is a cat, it must be able to catch the mouse
    - If the robot is a mouse, it must be able to escape the cat

We have several levels of objectives to achieve:
- Level 0: Robot moves + does not fall off the table
- Level 1: Detects another robot and either approaches it (cat) or moves away (mouse)
- Level 2: Changes behavior after contact + works with multiple robots
- Level 3: Capable of localizing itself + is unaffected by off-table obstacles

The project is to be completed over a semester, from September to January, with a certain number of deliverables due before each key milestone. The various technical stages include design, development, and validation phases on an embedded system.

<details>
<summary><strong>Detailed Plan</strong></summary>

### Before the All Saints' holiday

The first 10 sessions are dedicated to creating the PCB, which must be ordered before the All Saints' holiday.

- Session 1 → Architectural diagram / BOM
- Sessions 2 and 3 → Annotated electronic schematic
- Session 4 → Schematic corrections / Final BOM
- Session 5 → Placement
- Session 6 → Corrected placement
- Session 7 → Routing
- Sessions 8, 9, and 10 → Routing corrections, export

At the same time, we started the software part by creating the project on CubeIDE. We configured the pins and began writing libraries for the different components.

### Between All Saints' and Christmas

This period focuses on software development and integration.

### After the Christmas break

The focus is on the final adjustments and final testing before the presentation. Indeed, the last sessions dedicated to this project will allow us to finalize the strategy algorithms and robotic behaviors. The final challenge will take place on Friday, January 10, which will involve testing and presenting the project where all our class's robot cats will compete.

</details>

## Architectural Diagram and Materials

<div align="center">

</div>

Most of the materials were imposed on us, but we had to find our own method for detecting the edges so as not to fall off the table. 

For this, we would like to use IR sensors. This sensor will be placed under the robot and will receive a voltage that determines its distance from the ground. When this signal drops significantly (i.e., the distance increases), it means we're on an edge. Since it will be under the robot, we need a sensor capable of detecting short distances, like the Sharp GP2Y0A21SK0F sensor.

We would also like to add a visible LED that would allow us to know the state of our robot cat.

# PCB

The first step in designing our PCB was to create the electronic schematic of our board. Here's a list of the components used:

- **Microcontroller**: STM32G431CBU6
- **Voltage regulators**: 5V and 3.3V
- **Motor drivers**: ZXBM5210-SP-13
- **Battery system**: NIMH 7.2V 1.3Ah
- **ST Link**: Programming and debugging interface
- **Quartz oscillator**: 16MHz
- **Connectors**: Various connectors for power and signals
- **Accelerometer**: ADXL343

## Component and Wiring Details

### 1. Microcontroller: STM32G431CBU6

The STM32G431x6 microcontroller is at the heart of the robot. It handles the game logic and communicates with other components. The microcontroller's wiring diagram is available [here](./Documents/datasheets/stm32g431cb.pdf).

<div align="center">

</div>

The main connections include:
- **VDDA**: Connected to an LC filter to smooth the analog power supply.
- **VSS / VDD**: Main power supplies.
- **GPIOs**: Used for controlling debug LEDs and communicating with the motor drivers.

To configure the microcontroller pins, we use the CubeIDE software. Once the configuration is done, we generate the `.ioc` file, which documents all the options chosen for each pin. Using the microcontroller's IOC file allows us to optimally choose each pin for the microcontroller's input/output.

### 2. LED

The robot has 7 LEDs connected to current-limiting resistors.

- **A red LED**: Indicates that the robot is the cat.
- **A blue LED**: Indicates that the robot is a mouse.
- **Two green LEDs**: These are debug LEDs.
- **A yellow LED**: 5V indicator.
- **A green LED**: 3.3V indicator.
- **A green LED**: 7.2V indicator.

<div align="center">

</div>

### 3. Buttons

The robot has two buttons:
- **NRST**: Reset button.
- **Mode**: Button to switch the robot's state between "cat" and "mouse."

<div align="center">

</div>

### 4. Motor Drivers: ZXBM5210-SP-13

The motor drivers control the DC motors used to move the robot. We use the ZXBM5210 driver, connected as per the [documentation](./Documents/datasheets/driver_ZXBM5210.pdf).

<div align="center">

</div>

The driver connections include:
- **Vref**: Reference voltage for speed control.
- **VDD**: Motor power supply.
- **Control inputs**: Connected to the microcontroller's GPIOs.

<div align="center">

</div>

### 5. Voltage Regulators

We use two voltage regulators to convert the battery power:

<div align="center">

</div>

1. **7.2V → 5V Regulator: MP1475S**
   - Built according to the [documentation](./Documents/datasheets/regulateur_MP1475S.pdf).
   - Provides a 5V output to power the LIDAR and edge sensors.
   - To ensure we get 5V, we added a yellow LED connected to a current-limiting resistor.

<div align="center">

</div>

2. **5V → 3.3V Regulator: BU33SD5WG-TR**
   - Built according to the [documentation](./Documents/datasheets/regulateur_buxxsd5wg-e.pdf).
   - Powers the microcontroller and the display with 3.3V.
   - To ensure we get 3V, we added a green LED connected to a current-limiting resistor.

<div align="center">

</div>

### 6. 16MHz Quartz Oscillator

The quartz oscillator provides a stable clock for the microcontroller. It is connected according to the standard schematic, with decoupling capacitors.

<div align="center">

</div>

### 7. ST Link

The ST Link is used for programming and debugging the STM32 microcontroller. It allows us to flash code to the microcontroller and ensure serial communication for debugging.

- **VCC**: Power supply for the ST Link (3.3V).
- **SWDIO / SWCLK**: Communication pins for debugging.
- **NRST**: Connected to the reset button for hardware reset during programming.

<div align="center">

</div>

### 8. Accelerometer: ADXL343

The ADXL343 accelerometer measures the robot's movements. It is connected to the microcontroller via **SPI** communication. We chose SPI because it offers faster and more reliable communication for our application. The wiring is based on the [documentation](./Documents/datasheets/accelerometre_adxl343.pdf).

<div align="center">

</div>

### 9. Connectors

The robot has several connectors for interfacing with different peripherals:

<div align="center">

</div>

1. **Motor Connectors**

- The motor connectors link the PCB to the DC motors used to move the robot.
- Each connector is connected to a ZXBM5210 motor driver for speed and direction control.

<div align="center">

</div>

2. **LIDAR Connector**

- The Lidar connector is used to interface a Lidar sensor to the robot, allowing for distance and obstacle detection.
- It is connected to one of the microcontroller's communication ports (SPI or UART).

<div align="center">

</div>

3. **Display Connector**

- The display connector allows the addition of a small screen to show the robot's status (cat or mouse).
- This connector is connected to the I2C interface of the microcontroller.

<div align="center">

</div>

4. **Edge Sensor Connector**

- The edge sensor is used to detect the table edges and prevent the robot from falling off.
- The sensor is intrinsically connected to a DAC.

<div align="center">

</div>

### 10. Battery

The robot is powered by a 7.4V LiPo battery, which supplies power to the voltage regulators for various circuit components, the documentation used is [here](./Documents/datasheets/batterie_0900766b81582941.pdf). To ensure we receive a 7.2V voltage, we added a green LED connected to a current-limiting resistor.

<div align="center">

</div>

# Code

  ## Code Documentation

[see the documentation](./Documents/Doxygen_Documentation/html/index.html)
  
  ## Introduction

  In the context of this project, we need to use several communication methods such as SPI for the accelerometer and I2C for the OLED display.
  
  ## Lidar X4 Driver
  
  The `X4_driver.c` file provides an implementation to interface with the X4 device via UART communication. This driver supports various features, including starting and stopping scans, retrieving device information and status, and processing scan data. The driver uses a protocol defined in the `X4_driver.h` header file and handles responses from the X4 device.
  
  - **STM32 HAL library** for UART communication.
  - **Standard C libraries** (string.h, math.h, stdlib.h, stdbool.h).
  
  <details>
    <summary><strong>X4_driver.h Header File</strong></summary>
  
  ### Header File: `X4_driver.h`
  
  #### Macros
  
    - **Command Bytes:**
      - `X4_CMD_START` - Start a command sequence.
      - `X4_CMD_START_SCAN` - Command to start a scan.
      - `X4_CMD_STOP_SCAN` - Command to stop a scan.
      - `X4_CMD_GET_INFO` - Command to get device information.
      - `X4_CMD_GET_HEALTH` - Command to get device health status.
      - `X4_CMD_SOFT_RESTART` - Command to perform a soft restart.
  
    - **Response Protocol:**
      - `X4_RESPONSE_START_SIGN` - Expected start signature of a response.
      - `X4_RESPONSE_SINGLE_MODE` - Single response mode.
      - `X4_RESPONSE_CONTINUOUS_MODE` - Continuous response mode.
  
    - **Response Sizes:**
      - `X4_RESPONSE_HEADER_SIZE` - Size of the response header.
      - `X4_MAX_RESPONSE_SIZE` - Maximum size of the response content.
      - `X4_SERIAL_NUMBER_SIZE` - Size of the serial number.
      - `X4_SERIAL_FIRMWARE_SIZE` - Size of the firmware version.
  
  #### Structures
  
    - **`X4_ResponseMessage`**
      - Contains fields for parsing the response message, including the start signature, response length, mode, type code, and content.
  
    - **`X4_DeviceInfo`**
      - Contains fields for device model, firmware version, hardware version, and serial number.
  
    - **`X4_ScanData`**
      - Contains fields for packet header, packet type, number of samples, angles, checksum, and dynamically allocated sample data for distances and angles.
  
  #### Function Prototypes
  
    - **`void X4_StartScan(void);`**
      - Starts a scan on the X4 device.
  
    - **`void X4_StopScan(void);`**
      - Stops an ongoing scan.
  
    - **`void X4_GetDeviceInfo(void);`**
      - Retrieves device information.
  
    - **`void X4_GetHealthStatus(void);`**
      - Retrieves device health status.
  
    - **`void X4_SoftRestart(void);`**
      - Performs a soft restart of the device.
  
    - **`void X4_HandleResponse(void);`**
      - Handles the response received from the X4 device.
  
    - **`void X4_ParseMessage(const uint8_t *raw_data, X4_ResponseMessage *response);`**
      - Parses raw data into a structured response.
  
    - **`uint16_t convertBytesToUint16(const uint8_t* byte_array);`**
      - Converts a 2-byte array into an unsigned 16-bit integer.
    
  </details>
  
  <details>
    <summary><strong>X4_driver.c Source File</strong></summary>
  
  ### Key Functions
  
    - **`static void X4_SendCommand(uint8_t command)`**
      - Sends a command to the X4 device via UART.
  
    - **`void X4_StartScan(void)`**
      - Sends the start scan command and handles the response.
  
    - **`void X4_StopScan(void)`**
      - Sends the stop scan command.
  
    - **`void X4_SoftRestart(void)`**
      - Sends the soft restart command.
  
    - **`void X4_GetDeviceInfo(void)`**
      - Sends the command to get device information and processes the response.
  
    - **`void X4_GetDeviceHealth(void)`**
      - Sends the command to get device health status and processes the response.
  
    - **`void X4_HandleDeviceInfoResponse(const X4_ResponseMessage* response)`**
      - Handles and parses the device information response.
  
    - **`void X4_HandleDeviceHealthResponse(const X4_ResponseMessage* response)`**
      - Handles and parses the device health response.
  
    - **`void X4_HandleScanResponse(const X4_ResponseMessage* response)`**
      - Handles and parses scan data response.
  
    - **`void X4_HandleResponse(void)`**
      - Receives and processes UART data, sending it to the appropriate handler.
  
    - **`void X4_ParseMessage(const uint8_t *raw_data, X4_ResponseMessage *response)`**
      - Parses raw data into a structured response.
  
    - **`void X4_HandleScanDataDistances(X4_ScanData *scan_data)`**
      - Processes and calculates distances from scan data.
  
    - **`void X4_HandleScanDataAngles(X4_ScanData *scan_data)`**
      - Processes and calculates angles from scan data.
  
    - **`uint16_t calculateXOR(const X4_ScanData *scan_data, size_t packet_length)`**
      - Calculates the XOR of all bytes in the packet except the checksum.
  
    - **`bool verifyCheckCode(const X4_ScanData *scan_data, size_t packet_length)`**
      - Verifies scan data integrity using the checksum.
  
    - **`uint16_t convertBytesToUint16(const uint8_t* byte_array)`**
      - Converts a 2-byte array into an unsigned 16-bit integer.
  </details>
  
  <details>
    <summary><strong>Usage </strong></summary>
    
    1. **Initialization:**
       - Ensure that UART is properly initialized and configured in your main application.
  
    2. **Sending Commands:**
       - Use functions like `X4_StartScan()`, `X4_StopScan()`, and `X4_GetDeviceInfo()` to interact with the X4 device.
  
    3. **Handling Responses:**
       - Call `X4_HandleResponse()` to receive and process responses. Implement appropriate handlers for device information, device health, and scan data.
  
    4. **Processing Scan Data:**
       - Use `X4_HandleScanDataDistances()` and `X4_HandleScanDataAngles()` to process scan data and calculate distances and angles.
  </details>
  
  <details>
    <summary><strong>Notes </strong></summary>
    
  ### Notes
  
    - Ensure that the `HAL_UART_Receive` function is configured with an appropriate timeout and error handling for your application's needs.
    - Adjust `X4_MAX_RESPONSE_SIZE` in the header file as needed based on the expected response size from the device.
  </details>

##

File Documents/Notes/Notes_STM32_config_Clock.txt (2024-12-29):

[LIDAR]
M_SCTR (pour controler vitesse rotation) PWM à 10 kHZ

[ADC SENSORS]
sharp sensor measuring cycle : 16,5 ms
sysclock stm32 = 170 Mhz
Total conversion time adc = 0.25 -> 10.883 us

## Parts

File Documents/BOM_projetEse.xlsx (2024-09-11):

Composants | Nombre de composants | Reference fabricant | Datasheet | Voltage
Microcontrôleur | 1 | STM32G431CBU6 | https://www.st.com/resource/en/datasheet/stm32g431cb.pdf
Quartz 16 MHz | 1 | Farnell : 3820205 | https://www.farnell.com/datasheets/3820205.pdf
Connecteur SWD/STLink | 1 | M50-3600742 | https://cdn.harwin.com/pdfs/M50-360.pdf
Driver moteur | 2 | Mouser : ZXBM5210-SP-13 | https://www.diodes.com/assets/Datasheets/ZXBM5210.pdf
Moteur | 2 | DfRobot FIT0520 | https://mm.digikey.com/Volume0/opasdata/d220001/medias/docus/2326/FIT0520_Web.pdf
Accéléromètre | 1 | ADXL343BCCZ-RL
Régulateur 5V | 1 | MP1475S
Régulateur 3.3V | 1 | BU33SD5WG-TR
Batterie NIMH 7.2V 1.3Ah | 1 | RS : 777-0377
Capteur bordure | 4 | RS : GP2Y0A41SK0F | https://fr.rs-online.com/web/p/capteurs-optiques-reflechissants/6666568?gb=s
Lidar | 1 | YDLIDAR X4
Connecteurs JST 2.54mm | ?
LED en 0603 | ?
R en 0603 | ?
C en 0603 | ?

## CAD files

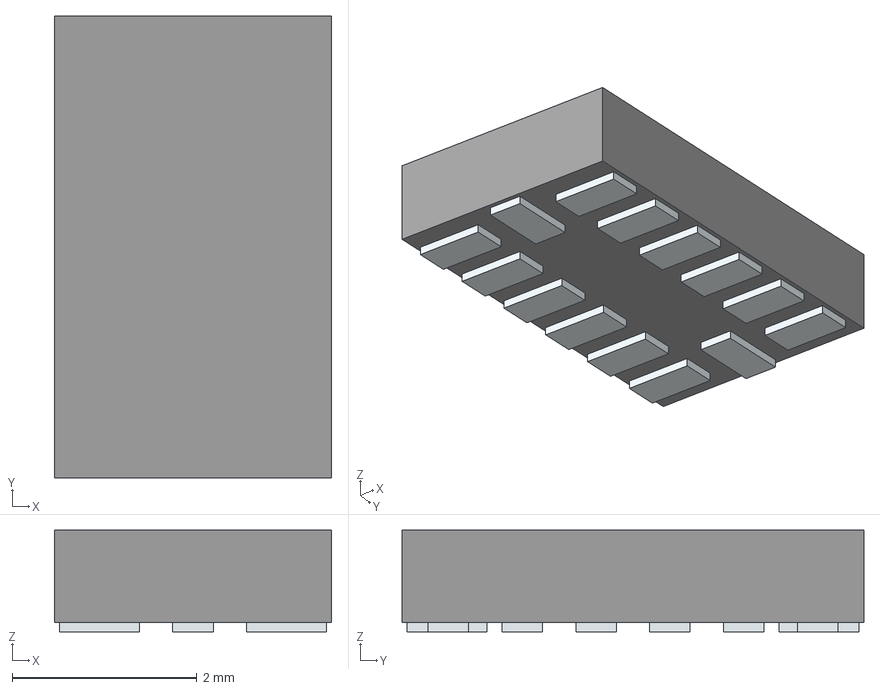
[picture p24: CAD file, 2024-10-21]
KiCad/TagBot/Ressources/ADXL343BCCZ-RL/3D/ADXL343BCCZ-RL.stp
3.00 x 5.00 x 1.10 mm
Pins

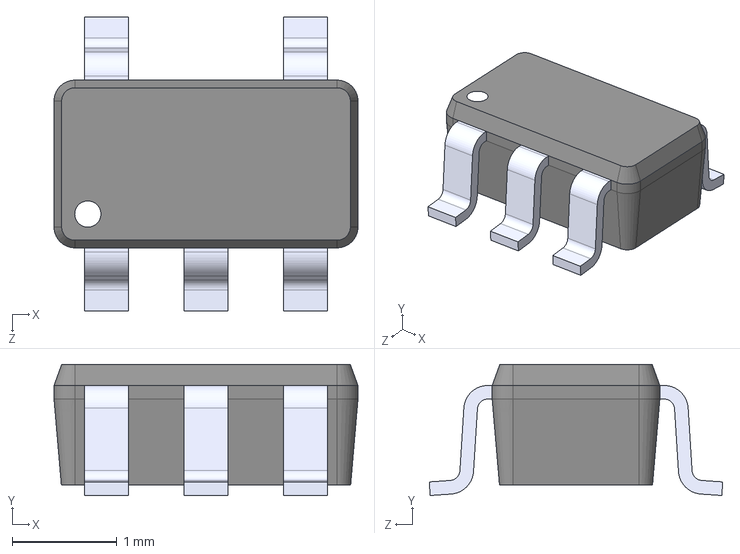
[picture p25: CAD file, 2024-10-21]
KiCad/TagBot/Ressources/BU33SD5WG-TR/BU33SD5WG-TR.step
2.90 x 1.25 x 2.80 mm

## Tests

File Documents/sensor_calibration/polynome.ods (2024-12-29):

x (en cm) | Y (en V)
3.5 | 3
4 | 2.72
5 | 2.3
6 | 2.015
7 | 1.77
8 | 1.57
9 | 1.4
10 | 1.25
12 | 1.15
14 | 0.95
16 | 0.81
18 | 0.75
20 | 0.65
25 | 0.53
30 | 0.42
35 | 0.385
40 | 0.32

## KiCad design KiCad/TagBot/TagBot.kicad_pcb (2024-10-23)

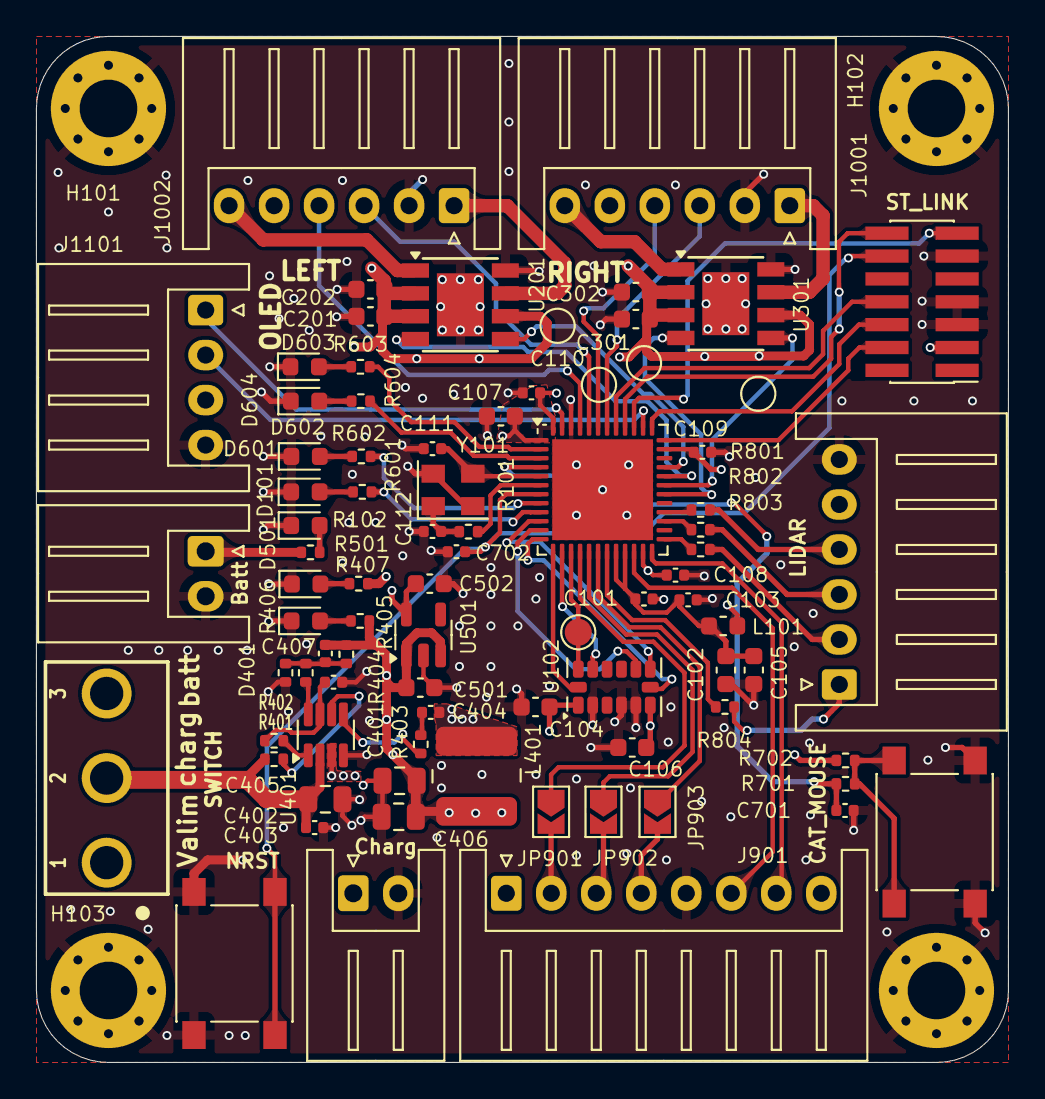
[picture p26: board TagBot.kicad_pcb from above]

Board: 4 copper layers, 54.0 x 57.0 mm, 87 parts (1 on the bottom side), 73 nets.

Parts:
Batt: Battery; JST_XH_S2B-XH-A_1x02_P2.50mm_Horizontal
C101, C108, C109, C110, C702: 100n; C_0402_1005Metric
C102, C104, C105, C106, C201, C301, C501, C502: 1u; C_0603_1608Metric
C103, C701: 10n; C_0402_1005Metric
C107: 4.7u; C_0603_1608Metric
C111, C112: 10p; C_0402_1005Metric
C202, C302: 10u; C_0603_1608Metric
C401, C403, C404: 0.1u; C_0402_1005Metric
C402, C405, C406: 22u; C_0805_2012Metric
C407: 15p; C_0402_1005Metric
CAT_MOUSE: SW_Push; SW_Push_1P1T_NO_6x6mm_H9.5mm
Charg: Conn_01x02; JST_XH_S2B-XH-A_1x02_P2.50mm_Horizontal
D101, D401, D501, D601, D602, D603, D604: LED; LED_0603_1608Metric
H101, H102, H103, H104: MountingHole_Pad; MountingHole_3.2mm_M3_Pad_Via
J901: Conn_01x08; JST_XH_S8B-XH-A_1x08_P2.50mm_Horizontal
J1001, J1002: Conn_01x06; JST_XH_S6B-XH-A_1x06_P2.50mm_Horizontal
J1101: Conn_01x04; JST_XH_S4B-XH-A_1x04_P2.50mm_Horizontal
JP901, JP902, JP903: SolderJumper_2_Open; SolderJumper-2_P1.3mm_Open_TrianglePad1.0x1.5mm
L101: 39n; L_0603_1608Metric
L401: 4.7u; Power Inductors - SMD WE-LQS 4.7uH
LEFT_REV: TestPoint; TestPoint_Pad_D1.5mm
LIDAR: Conn_01x06; JST_XH_S6B-XH-A_1x06_P2.50mm_Horizontal
MISO: TestPoint; TestPoint_Pad_D1.5mm
MOSI101: TestPoint; TestPoint_Pad_D1.5mm
NRST: SW_Push; SW_Push_1P1T_NO_6x6mm_H9.5mm
R101: 10; R_0402_1005Metric
R102: 4k; R_0402_1005Metric
R401, R402: 100k; R_0402_1005Metric
R403: 20; R_0402_1005Metric
R404: 16k; R_0402_1005Metric
R405: 40.2k; R_0402_1005Metric
R406: 7.68k; R_0402_1005Metric
R407: 3k; R_0402_1005Metric
R501, R601, R602, R604: 300; R_0402_1005Metric
R603: 1.3k; R_0402_1005Metric
R701, R702: 10k; R_0402_1005Metric
R801, R802, R803, R804: 100; R_0402_1005Metric
RIGHT_FWD: TestPoint; TestPoint_Pad_D1.5mm
RIGHT_REV: TestPoint; TestPoint_Pad_D1.5mm
ST_LINK: Conn_ST_STDC14; PinHeader_2x07_P1.27mm_Vertical_SMD
TPLEFT_FWD: TestPoint; TestPoint_Pad_D1.5mm
U101: STM32G431CBUx; QFN-48-1EP_7x7mm_P0.5mm_EP5.6x5.6mm
U102: ADXL343; LGA-14_3x5mm_P0.8mm_LayoutBorder1x6y
U201, U301: ZXBM5210-SP; Diodes_SO-8EP
U401: MP1475S; TSOT-23-8
U501: BU33SD5WG-TR; SOT-23-5
Y101: Crystal; Crystal_SMD_EuroQuartz_MT-4Pin_3.2x2.5mm
charg: switch; 472121020311

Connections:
+3.3V: C104.2, C106.2, C107.1, C108.1, C109.1, C110.1, C502.1, J1001.5, J1002.5, J1101.3, L101.1, R501.1, R702.1, ST_LINK.3 (VCC), U101.1 (VBAT), U101.23 (VDD), U101.35 (VDD), U101.48 (VDD), U102.1 (Vdd_I/O), U102.6 (Vs), U501.5 (VOUT)
+3.3VA: C101.2, C102.2, C103.2, C105.2, L101.2, U101.20 (VREF+), U101.21 (VDDA)
+5V: C405.1, C406.1, C407.2, C501.1, J901.8, L401.2, LIDAR.5, R405.2, R407.1, U501.1 (VIN), U501.3 (~SHDN)
/BTN_CAT_MOUSE: C701.1, R701.2, U101.4 (PC15)
/CS-NSS: U101.12 (PA4), U102.7 (~CS)
/Capteur_dist_E: R801.1, U101.28 (PB15)
/Capteur_dist_N: R803.1, U101.25 (PB12)
/Capteur_dist_S: R804.1, U101.19 (PB2)
/Capteur_dist_W: R802.1, U101.27 (PB14)
/DEV_EN: JP902.1 (A), U101.17 (PB0)
/Encoder_Left_A: J1002.3, U101.44 (PB6)
/Encoder_Left_B: J1002.4, U101.45 (PB7)
/Encoder_Right_A: J1001.3, U101.42 (PB4)
/Encoder_Right_B: J1001.4, U101.43 (PB5)
/Interrupt1: U101.10 (PA2), U102.8 (INT1)
/Interrupt2: U101.11 (PA3), U102.9 (INT2)
/LED_chat: R603.2, U101.2 (PC13)
/LED_souris: R604.2, U101.3 (PC14)
/LEFT_FWD: TPLEFT_FWD.1, U101.32 (PA10), U201.4 (FWD)
/LEFT_OUT1: J1002.6, U201.1 (OUT1)
/LEFT_OUT2: J1002.1, U201.7 (OUT2)
/LEFT_REV: LEFT_REV.1, U101.33 (PA11), U201.5 (REV)
/LIDAR_Input: J901.6, U101.22 (PB10)
/LIDAR_Output: J901.7, U101.24 (PB11)
/M_EN: JP901.1 (A), U101.16 (PC4)
/M_SCTR: JP903.1 (A), U101.18 (PB1)
/NRST: C702.1, NRST.1, ST_LINK.12 (~RST), U101.7 (PG10)
/OLED_SCL: J1101.2, U101.38 (PA15)
/OLED_SDA: J1101.1, U101.47 (PB9)
/OSC_in: C111.1, U101.5 (PF0), Y101.3
/OSC_out: R101.2, U101.6 (PF1)
/RIGHT_FWD: RIGHT_FWD.1, U101.30 (PA8), U301.4 (FWD)
/RIGHT_OUT1: J1001.6, U301.1 (OUT1)
/RIGHT_OUT2: J1001.1, U301.7 (OUT2)
/RIGHT_REV: RIGHT_REV.1, U101.31 (PA9), U301.5 (REV)
/SCLK-SCK: U101.13 (PA5), U102.14 (SCL/SCLK)
/SDI-MOSI: MOSI101.1, U101.15 (PA7), U102.13 (SDA/SDI/SDIO)
/SDO-MISO: MISO.1, U101.14 (PA6), U102.12 (SDO/ADDR)
/STLINK_RX: ST_LINK.14 (VCP_TX), U101.40 (PC11)
/STLINK_TX: ST_LINK.13 (VCP_RX), U101.39 (PC10)
/SYS_JTCK-SWCLK: ST_LINK.6 (JCLK/SWCLK), U101.37 (PA14)
/SYS_JTDO-SWO: ST_LINK.8 (JTDO/SWO), U101.41 (PB3)
/SYS_JTMS-SWDIO: ST_LINK.4 (JTMS/SWDIO), U101.36 (PA13)
/USR_LED_1: R602.2, U101.8 (PA0)
/USR_LED_2: R601.2, U101.9 (PA1)
/Valim: C201.2, C202.2, C301.2, C302.2, C402.1, C403.1, R401.1, U201.2 (VM), U201.3 (VDD), U201.6 (VREF), U301.2 (VM), U301.3 (VDD), U301.6 (VREF), U401.2 (In), charg.2 (C)
/Vbatterie: Batt.1 (+), R102.1, charg.3 (A)
GND: Batt.2 (-), C101.1, C102.1, C103.1, C104.1, C105.1, C106.1, C107.2, C108.2, C109.2, C110.2, C111.2, C112.2, C201.1, C202.1, C301.1, C302.1, C401.2, C402.2, C403.2, C405.2, C406.2, C501.2, C502.2, C701.2, C702.2, CAT_MOUSE.2, Charg.2, D101.1 (K), D401.1 (K), D501.1 (K), D601.1 (K), D602.1 (K), D603.1 (K), D604.1 (K), H101.1, H102.1, H103.1, H104.1, J901.5, J1001.2, J1002.2, J1101.4, LIDAR.6, NRST.2, R406.2, ST_LINK.5 (GND), ST_LINK.7 (GND), ST_LINK.11 (GNDDetect), U101.46 (PB8), U101.49 (VSS), U102.2 (GND), U102.4 (GND), U102.5 (GND), U201.8 (GND), U201.9 (GND), U301.8 (GND), U301.9 (GND), U401.4 (GND), U501.2 (GND), Y101.2, Y101.4
unnamed: C112.1, R101.1, Y101.1
unnamed: C404.1, R403.2
unnamed: C407.1, R404.2, R405.1, R406.1
unnamed: D101.2 (A), R102.2
unnamed: D401.2 (A), R407.2
unnamed: D501.2 (A), R501.2
unnamed: D601.2 (A), R601.1
unnamed: D602.2 (A), R602.1
unnamed: D603.2 (A), R603.1
unnamed: D604.2 (A), R604.1
unnamed: Charg.1, charg.1 (B)
unnamed: LIDAR.1, R804.2
unnamed: LIDAR.2, R803.2
unnamed: LIDAR.3, R802.2
unnamed: LIDAR.4, R801.2
unnamed: J901.2, JP901.2 (B)
unnamed: J901.3, JP902.2 (B)
unnamed: J901.4, JP903.2 (B)
unnamed: CAT_MOUSE.1, R701.1, R702.2
unnamed: R403.1, U401.5 (BST)
unnamed: R401.2, U401.6 (EN/SYNC)
unnamed: R404.1, U401.8 (FB)
unnamed: R402.2, U401.1 (PG)
unnamed: C404.2, L401.1, U401.3 (SW)
unnamed: C401.1, R402.1, U401.7 (VCC)

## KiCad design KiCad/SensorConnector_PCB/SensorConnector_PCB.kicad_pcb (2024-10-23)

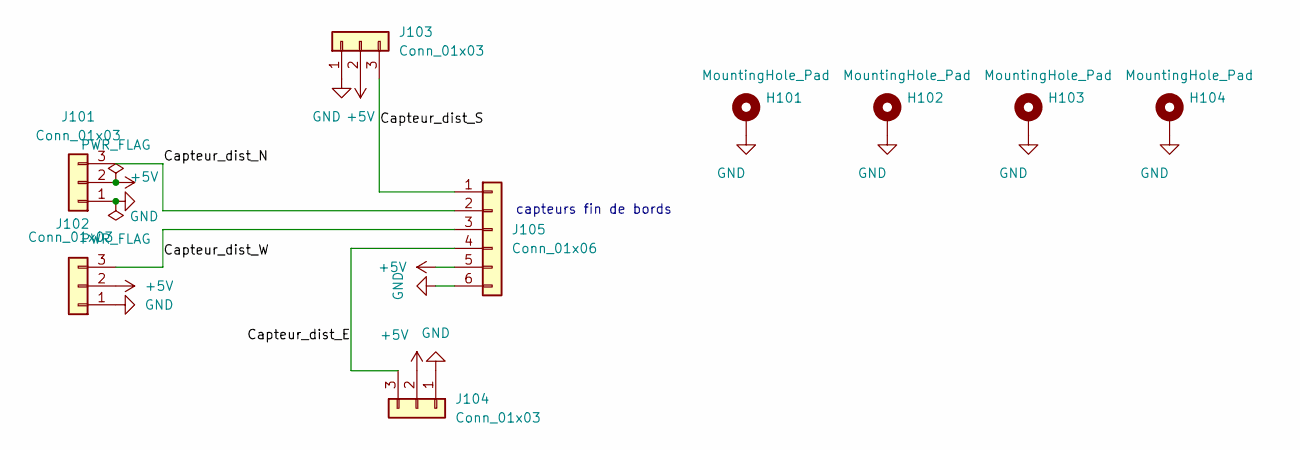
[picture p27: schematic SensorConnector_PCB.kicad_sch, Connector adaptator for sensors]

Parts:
H101, H102, H103, H104: MountingHole_Pad; MountingHole_3.2mm_M3_Pad_Via
J101, J102, J103, J104: Conn_01x03; JST_XH_S3B-XH-A_1x03_P2.50mm_Horizontal
J105: Conn_01x06; JST_XH_S6B-XH-A_1x06_P2.50mm_Horizontal

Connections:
+5V: J101.2, J102.2, J103.2, J104.2, J105.5
/Capteur_dist_E: J104.3, J105.4
/Capteur_dist_N: J101.3, J105.2
/Capteur_dist_S: J103.3, J105.1
/Capteur_dist_W: J102.3, J105.3
GND: H101.1, H102.1, H103.1, H104.1, J101.1, J102.1, J103.1, J104.1, J105.6

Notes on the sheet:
capteurs fin de bords

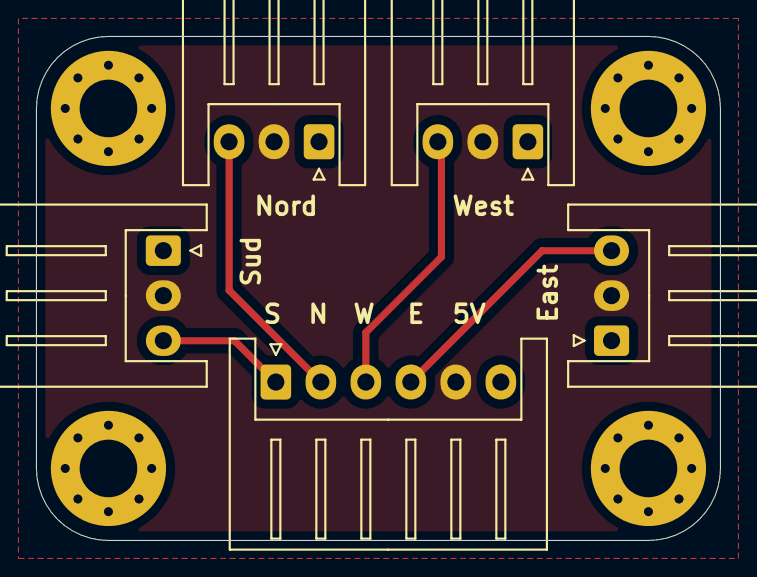
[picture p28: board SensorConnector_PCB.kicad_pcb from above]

Board: 2 copper layers, 38.0 x 28.0 mm, 9 parts (0 on the bottom side), 6 nets.

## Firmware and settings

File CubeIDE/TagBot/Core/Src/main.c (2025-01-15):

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
/* Includes ------------------------------------------------------------------*/
#include "main.h"
#include "cmsis_os.h"
#include "adc.h"
#include "dma.h"
#include "i2c.h"
#include "spi.h"
#include "tim.h"
#include "usart.h"
#include "gpio.h"

/* USER CODE BEGIN Includes */
#include "stm32g4xx_hal.h"
#include "semphr.h"
#include "X4LIDAR_driver.h"
#include "DCMotor_driver.h"
#include "SSD1306.h"
#include "SSD1306_fonts.h"
#include "shell.h"
#include "RobotStrategy.h"
#include "distSensor_driver.h"
#include "ADXL343_driver.h"
/* USER CODE END Includes */

/* USER CODE BEGIN PD */
#define DISTANCE_SENSOR_ADC_BUFFER_SIZE 10
/* USER CODE END PD */


/* USER CODE BEGIN PV */
X4LIDAR_handle_t X4LIDAR_handle;
DualDrive_handle_t DualDrive_handle;
__TARGET_HandleTypeDef Target_Handle;


/* USER CODE END PV */

void SystemClock_Config(void);
void MX_FREERTOS_Init(void);
/* USER CODE BEGIN 0 */
int __io_putchar(int ch)
{
	// Send the character using HAL_UART_Transmit
	HAL_UART_Transmit(&huart4, (uint8_t*) &ch, 1, HAL_MAX_DELAY);

	return ch;  // Return the character back to the caller
}

void print_lidar_distances(h_shell_t *h_shell, int argc, char **argv)
{
	for (int i = MIN_ANGLE; i < MAX_ANGLE; i++)
	{
		printf("%s %d: %f \r\n",
				"angle ", i,  X4LIDAR_handle.scan_data.distances[i]);
	}
}

void print_motor_speed(h_shell_t *h_shell, int argc, char **argv)
{
	uint32_t speed_left = DualDrive_handle.motor_left.encoder.measured_rpm;
	uint32_t speed_right = DualDrive_handle.motor_right.encoder.measured_rpm;

	printf("speed left = %lu \r\n", speed_left);
	printf("speed right = %lu \r\n", speed_right);
}



void vApplicationStackOverflowHook(TaskHandle_t xTask, char *pcTaskName)
{
	Error_Handler();
}
/* USER CODE END 0 */

/**
  * @brief  The application entry point.
  * @retval int
  */
int main(void)
{

  /* USER CODE BEGIN 1 */
	//to disable timer in debug mode

	//to disable timer in debug mode

  /* USER CODE END 1 */

  /* MCU Configuration--------------------------------------------------------*/

  /* Reset of all peripherals, Initializes the Flash interface and the Systick. */
  HAL_Init();

  /* Configure the system clock */
  SystemClock_Config();

  /* Initialize all configured peripherals */
  MX_GPIO_Init();
  MX_DMA_Init();
  MX_UART4_Init();
  MX_SPI1_Init();
  MX_TIM4_Init();
  MX_ADC1_Init();
  MX_ADC2_Init();
  MX_TIM1_Init();
  MX_TIM3_Init();
  MX_USART3_UART_Init();
  MX_I2C1_Init();
  MX_TIM6_Init();
  MX_TIM8_Init();
  /* USER CODE BEGIN 2 */
	printf(" _____________________________\r\n");
	printf("|                             |\r\n");
	printf("|                             |\r\n");
	printf("|  WELCOME ON TAGBOT PROJECT  |\r\n");
	printf("|                             |\r\n");
	printf("|_____________________________|\r\n");
	//**********************************************************

	/* Ce code initialise l'adc en dma*/
	distSensor_TaskCreate(NULL);
	printf("Démarrage du test des capteurs de distance...\r\n");

	//**********************************************************

	/* Code init l'accélérometre*/

/*Ce code a été bougé au début de la task donc pas besoin ici

	while(1 == ADXL343_Init()) {}
	ADXL343_Configure();*/

	ADXL343_TaskCreate(NULL);
	printf("adxl task creat \r\n");

	//**********************************************************
	DCMotor_CreateTask(&DualDrive_handle);
	printf("dcmotor task creat \r\n");

	//**********************************************************
	// Init SCREEN OLED
	if(HAL_OK == SCREEN_SSD1306_Init(&hscreen1, &hi2c1))
	{
		SCREEN_SSD1306_DrawBitmap(&hscreen1, Nyan_115x64px, 115, 64, White);
		//SCREEN_SSD1306_DrawBitmap(&hscreen1, Jerry_50x64px, 120, 64, White);
		SCREEN_SSD1306_Update_Screen(&hscreen1);
	}
	//**********************************************************
	//LIDAR

	X4LIDAR_create_task(&X4LIDAR_handle);
	printf("lidar task creat \r\n");
	//**********************************************************
//	shell_init(&h_shell);
//	shell_add(&h_shell, "print_dist", print_lidar_distances,
//			"print lidar buffer containing scanned distances");
//	shell_add(&h_shell, "print_motor_speed", print_motor_speed,
//			"print_motor_speed");
//	shell_createShellTask(&h_shell);

	//**********************************************************
	RobotStrategy_CreateTask();

	//**********************************************************

	//HAL_Delay(20000);
	//**********************************************************

	printf("Tasks creation finished... \r\n");
	//**********************************************************

  /* USER CODE END 2 */

  /* Call init function for freertos objects (in cmsis_os2.c) */
  MX_FREERTOS_Init();

  /* Start scheduler */
  osKernelStart();

  /* We should never get here as control is now taken by the scheduler */

  /* Infinite loop */
  /* USER CODE BEGIN WHILE */
	while (1)
	{
    /* USER CODE END WHILE */

    /* USER CODE BEGIN 3 */
	}
  /* USER CODE END 3 */
}

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
/* USER CODE BEGIN 4 */


void HAL_UART_RxHalfCpltCallback(UART_HandleTypeDef *huart)
{

	X4LIDAR_HAL_UART_RxHalfCpltCallback(huart,&X4LIDAR_handle);

}

void HAL_UART_RxCpltCallback(UART_HandleTypeDef *huart)
{

	shell_drv_uart_HAL_UART_RxCpltCallback(huart);
	X4LIDAR_HAL_UART_RxCpltCallback(huart,&X4LIDAR_handle);

}

void HAL_UART_TxCpltCallback(UART_HandleTypeDef *huart)
{
	shell_drv_uart_HAL_UART_TxCpltCallback(huart);
}
/* USER CODE END 4 */

/**
  * @brief  Period elapsed callback in non blocking mode
  * @note   This function is called  when TIM7 interrupt took place, inside
  * HAL_TIM_IRQHandler(). It makes a direct call to HAL_IncTick() to increment
  * a global variable "uwTick" used as application time base.
  * @param  htim : TIM handle
  * @retval None
  */
void HAL_TIM_PeriodElapsedCallback(TIM_HandleTypeDef *htim)
{
  if (htim->Instance == TIM7) {
    HAL_IncTick();
  }
  /* USER CODE BEGIN Callback 1 */
	  DCMotor_EncoderCallback(htim ,&DualDrive_handle);


  /* USER CODE END Callback 1 */
}

/**
  * @brief  This function is executed in case of error occurrence.
  * @retval None
  */
void Error_Handler(void)
{
  /* USER CODE BEGIN Error_Handler_Debug */
	/* User can add his own implementation to report the HAL error return state */
	__disable_irq();
	while (1)
	{
	}
  /* USER CODE END Error_Handler_Debug */
}

#ifdef  USE_FULL_ASSERT
/**
  * @brief  Reports the name of the source file and the source line number
  *         where the assert_param error has occurred.
  * @param  file: pointer to the source file name
  * @param  line: assert_param error line source number
  * @retval None
  */
void assert_failed(uint8_t *file, uint32_t line)
{
  /* USER CODE BEGIN 6 */
	/* User can add his own implementation to report the file name and line number,
     ex: printf("Wrong parameters value: file %s on line %d\r\n", file, line) */
  /* USER CODE END 6 */
}
#endif /* USE_FULL_ASSERT */

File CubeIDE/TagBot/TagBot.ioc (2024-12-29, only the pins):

Mcu.UserName=STM32G431CBUx
PA0.GPIO_Label=USER_LED_1
PA0.Signal=GPIO_Output
PA1.GPIO_Label=USER_LED_2
PA1.Signal=GPIO_Output
PA10.GPIO_Label=LEFT_MOTOR_FWD
PA10.Signal=S_TIM1_CH3
PA11.GPIO_Label=LEFT_MOTOR_REV
PA11.Signal=S_TIM1_CH4
PA13.Signal=SYS_JTMS-SWDIO
PA14.Signal=SYS_JTCK-SWCLK
PA15.Signal=I2C1_SCL
PA2.GPIO_Label=Accelerometer_INT1
PA2.Signal=GPXTI2
PA3.GPIO_Label=Accelerometer_INT2
PA3.Signal=GPXTI3
PA4.GPIO_Label=Accelerometer_NSS
PA4.Signal=GPIO_Output
PA5.GPIO_Label=Accelerometer_SCK
PA5.Signal=SPI1_SCK
PA6.GPIO_Label=Accelerometer_MISO
PA6.Signal=SPI1_MISO
PA7.GPIO_Label=Accelerometer_MOSI
PA7.Signal=SPI1_MOSI
PA8.GPIO_Label=RIGHT_MOTOR_FWD
PA8.Signal=S_TIM1_CH1
PA9.GPIO_Label=RIGHT_MOTOR_REV
PA9.Signal=S_TIM1_CH2
PB0.GPIO_Label=LIDAR_DEV_EN
PB0.Signal=GPIO_Output
PB10.GPIO_Label=LIDAR_INPUT
PB10.Signal=USART3_TX
PB11.GPIO_Label=LIDAR_OUTPUT
PB11.Signal=USART3_RX
PB12.GPIO_Label=CAPTEUR_DIST_N
PB12.Signal=ADC1_IN11
PB14.GPIO_Label=CAPTEUR_DIST_W
PB14.Signal=ADC1_IN5
PB15.GPIO_Label=CAPTEUR_DIST_E
PB15.Signal=ADC2_IN15
PB2.GPIO_Label=CAPTEUR_DIST_S
PB2.Signal=ADC2_IN12
PB3.Signal=SYS_JTDO-SWO
PB4.GPIO_Label=ENCODER_RIGHT_A
PB4.Signal=S_TIM3_CH1
PB5.GPIO_Label=ENCODER_RIGHT_B
PB5.Signal=S_TIM3_CH2
PB6.GPIO_Label=ENCODER_LEFT_A
PB6.Signal=S_TIM4_CH1
PB7.GPIO_Label=ENCODER_LEFT_B
PB7.Signal=S_TIM4_CH2
PB9.Signal=I2C1_SDA
PC10.GPIO_Label=STLINK_TX
PC10.Signal=UART4_TX
PC11.GPIO_Label=STLINK_RX
PC11.Signal=UART4_RX
PC13.GPIO_Label=LED_CHAT
PC13.Signal=GPIO_Output
PC14-OSC32_IN.GPIO_Label=LED_SOURIS
PC14-OSC32_IN.Signal=GPIO_Output
PC15-OSC32_OUT.GPIO_Label=BTN_CAT_MOUSE
PC15-OSC32_OUT.Signal=GPIO_Input
PC4.GPIO_Label=LIDAR_M_EN
PC4.Signal=GPIO_Output
PF0-OSC_IN.Signal=RCC_OSC_IN
PF1-OSC_OUT.Signal=RCC_OSC_OUT

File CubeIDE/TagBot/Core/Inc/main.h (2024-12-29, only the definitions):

#define LED_CHAT_Pin GPIO_PIN_13
#define LED_CHAT_GPIO_Port GPIOC
#define LED_SOURIS_Pin GPIO_PIN_14
#define LED_SOURIS_GPIO_Port GPIOC
#define BTN_CAT_MOUSE_Pin GPIO_PIN_15
#define BTN_CAT_MOUSE_GPIO_Port GPIOC
#define USER_LED_1_Pin GPIO_PIN_0
#define USER_LED_1_GPIO_Port GPIOA
#define USER_LED_2_Pin GPIO_PIN_1
#define USER_LED_2_GPIO_Port GPIOA
#define Accelerometer_INT1_Pin GPIO_PIN_2
#define Accelerometer_INT1_GPIO_Port GPIOA
#define Accelerometer_INT2_Pin GPIO_PIN_3
#define Accelerometer_INT2_GPIO_Port GPIOA
#define Accelerometer_NSS_Pin GPIO_PIN_4
#define Accelerometer_NSS_GPIO_Port GPIOA
#define Accelerometer_SCK_Pin GPIO_PIN_5
#define Accelerometer_SCK_GPIO_Port GPIOA
#define Accelerometer_MISO_Pin GPIO_PIN_6
#define Accelerometer_MISO_GPIO_Port GPIOA
#define Accelerometer_MOSI_Pin GPIO_PIN_7
#define Accelerometer_MOSI_GPIO_Port GPIOA
#define LIDAR_M_EN_Pin GPIO_PIN_4
#define LIDAR_M_EN_GPIO_Port GPIOC
#define LIDAR_DEV_EN_Pin GPIO_PIN_0
#define LIDAR_DEV_EN_GPIO_Port GPIOB
#define CAPTEUR_DIST_S_Pin GPIO_PIN_2
#define CAPTEUR_DIST_S_GPIO_Port GPIOB
#define LIDAR_INPUT_Pin GPIO_PIN_10
#define LIDAR_INPUT_GPIO_Port GPIOB
#define LIDAR_OUTPUT_Pin GPIO_PIN_11
#define LIDAR_OUTPUT_GPIO_Port GPIOB
#define CAPTEUR_DIST_N_Pin GPIO_PIN_12
#define CAPTEUR_DIST_N_GPIO_Port GPIOB
#define CAPTEUR_DIST_W_Pin GPIO_PIN_14
#define CAPTEUR_DIST_W_GPIO_Port GPIOB
#define CAPTEUR_DIST_E_Pin GPIO_PIN_15
#define CAPTEUR_DIST_E_GPIO_Port GPIOB
#define RIGHT_MOTOR_FWD_Pin GPIO_PIN_8
#define RIGHT_MOTOR_FWD_GPIO_Port GPIOA
#define RIGHT_MOTOR_REV_Pin GPIO_PIN_9
#define RIGHT_MOTOR_REV_GPIO_Port GPIOA
#define LEFT_MOTOR_FWD_Pin GPIO_PIN_10
#define LEFT_MOTOR_FWD_GPIO_Port GPIOA
#define LEFT_MOTOR_REV_Pin GPIO_PIN_11
#define LEFT_MOTOR_REV_GPIO_Port GPIOA
#define STLINK_TX_Pin GPIO_PIN_10
#define STLINK_TX_GPIO_Port GPIOC
#define STLINK_RX_Pin GPIO_PIN_11
#define STLINK_RX_GPIO_Port GPIOC
#define ENCODER_RIGHT_A_Pin GPIO_PIN_4
#define ENCODER_RIGHT_A_GPIO_Port GPIOB
#define ENCODER_RIGHT_B_Pin GPIO_PIN_5
#define ENCODER_RIGHT_B_GPIO_Port GPIOB
#define ENCODER_LEFT_A_Pin GPIO_PIN_6
#define ENCODER_LEFT_A_GPIO_Port GPIOB
#define ENCODER_LEFT_B_Pin GPIO_PIN_7
#define ENCODER_LEFT_B_GPIO_Port GPIOB

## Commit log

2024-09-11 added schematics
2024-09-11 added KiCad project
    [TagBot.kicad_pcb, TagBot.kicad_sch]
2024-09-11 modif kicad project
    [TagBot.kicad_sch]
2024-09-11 add BOM
    [BOM_projetEse.xlsx]
2024-09-11 changed gitignore for Kicad and Started CubeIde config
2024-09-12 started writing lidar driver
2024-09-13 handle sample point distance for lidar
2024-09-14 Lidar driver : added lidar angles functions and crc
2024-09-15 added Lidar driver documentation
2024-09-16 added driver files for motor and accleerometer to cubeide
2024-09-17 started pin config
    [ADXL343BCCZ-RL.stp]
2024-09-17 kicad and cubeide pin config
    [BU33SD5WG-TR.step, Driver.kicad_sch, DriverLeft.kicad_sch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]
2024-09-17 Kicad regulateur MP1475S
    [DriverLeft.kicad_sch, DriverRight.kicad_sch, Kicad_mariesversion.kicad_pcb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]
2024-09-18 boot0 of stm32 connected to gnd
    [DriverLeft.kicad_sch, TagBot.kicad_sch]
2024-09-18 update kicad
    [TagBot.kicad_sch]
2024-09-18 added I2C for display
2024-09-20 added push button to switch cat/mouse
2024-09-23 polyonme fitting for distance sensor values
    [polynome.ods]
2024-09-24 update footprint kicad
    [DriverLeft.kicad_sch, DriverRight.kicad_sch, TagBot.kicad_sch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]
2024-09-25 placement pcb
    [DriverLeft.kicad_sch, TagBot.kicad_pcb, TagBot.kicad_sch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]
2024-09-30 ajout résistance capteurs
    [TagBot.kicad_pcb, TagBot.kicad_sch]
2024-10-01 correction schema kicad
    [DriverLeft.kicad_sch, DriverRight.kicad_sch, TagBot.kicad_pcb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]
2024-10-02 Update README.md kicad
2024-10-02 placement pcb 2
    [ADXL343BCCZ-RL.stp, BU33SD5WG-TR.step, DriverLeft.kicad_sch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]
2024-10-02 Added connector pcb
    [SensorConnector_PCB.kicad_pcb, SensorConnector_PCB.kicad_sch]
2024-10-02 fixed silkscreen display of connector pcb
    [SensorConnector_PCB.kicad_pcb]
2024-10-06 updated pcb placement
    [TagBot.kicad_pcb]
2024-10-07 configured adc timer and dma
2024-10-07 Routed data tracks
    [TagBot.kicad_pcb]
2024-10-08 update routage
    [TagBot.kicad_pcb]
2024-10-09 update images kicad
2024-10-16 upadate pcb name
    [TagBot.kicad_pcb]
2024-10-22 added pictures for PCB description readme
2024-10-22 working get device info function
2024-10-22 correction routage
    [TagBot.kicad_pcb, TagBot.kicad_sch]
2024-10-22 update silkscreen
    [TagBot.kicad_pcb]
2024-10-22 update antenne
    [TagBot.kicad_pcb]
2024-10-22 fixed switch footprint and genrated gerber files
    [DriverLeft.kicad_sch, DriverRight.kicad_sch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]
2024-10-23 update pcb connector files
    [SensorConnector_PCB.kicad_pcb]
2024-10-23 Generated gerber files for Connector PCB
    [SensorConnector_PCB-B_Cu.gbr, SensorConnector_PCB-B_Mask.gbr, SensorConnector_PCB-B_Paste.gbr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]
2024-10-23 reduced solder by 15%
    [TagBot-B_Cu.gbr, TagBot-B_Mask.gbr, TagBot-B_Paste.gbr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]
2024-11-13 updated testing project for lidar
2024-11-17 WIP rework lidarl lib
    [Testing.ioc, main.c]
2024-11-19 workin ppz lidar lib with interrupt
2024-11-20 angles work with dma but distances don't
2024-11-21 WIP lidar lib testing
2024-11-21 test_func to debug DMA is working
2024-11-21 created new testing project to fix cubeide code generation
    [Testing.ioc, main.c]
2024-11-21 first successful data transfer DMA FreeRTOS
2024-11-23 switched to circular buffer, seems to be working
2024-11-24 lidar lib seems to be working, god is good
2024-11-24 shell task conflicts with lidar task WIP
2024-11-28 fixed an issue for the device info function
    [Testing.ioc, main.c]
2024-11-29 wip lidar
2024-11-30 working lidar lib, god is goood 👁 👅 👁
2024-12-03 encoder wip
2024-12-13 working motors
2024-12-16 Mise à jour de TagBot depuis la branche charlotte
2024-12-18 incorporation lidar doesn't work
    [main.c]
2024-12-19 motor and lidar wip
2024-12-19 lidar debug and motor ratio fixed
    [main.c]
2024-12-23 somewhat working steering, PID WIP for motors
2024-12-23 little commit before switching to PID motor
2024-12-29 removed obsolete lidar documentation from readme

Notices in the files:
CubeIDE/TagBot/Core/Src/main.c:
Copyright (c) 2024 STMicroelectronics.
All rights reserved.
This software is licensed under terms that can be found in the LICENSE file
